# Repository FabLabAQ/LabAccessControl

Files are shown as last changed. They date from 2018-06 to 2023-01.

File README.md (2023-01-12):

# LabAccessControl

## FabLab access and machine control system proof-of-concept
* We use this system to manage access to our laboratory and machines usage (3D printers, laser cutter, CNC mill, etc.).
* Maker friendly and customizable, based on ESP8266 and programmed through the Arduino IDE.
* The ESP retrieves an authorized RFID cards list from a Google sheet and stores that list on flash memory, only when that list changes the internal cards list is updated with minimum flash memory wearing.
* It also logs events (what happened, when, and eventually who) on an internal FIFO and sends these logs to another Google sheet when internet connection is available.
* Due to the features above, this system can work also when internet connection goes down.

# WARNING:
Don't use MIFARE Classic cards if you don't want unauthorized access, they are clonable. Use at least Ultralight C for secure encryption.

# Development
## TODO (urgent)
Common
- [ ] diversify card keys
- [ ] switch to msgpack instead of json

Firmware
- [ ] replace DES library
- [ ] implement DES key generation
- [ ] switch to incremental mode for db updates
- [ ] implement signed messages
- [ ] implement provisioning and recovery of keys (Tang-like)

Script
- [ ] unify sheets
- [ ] incremental updates
- [ ] provisioning and recovery

App
- [ ] signed messages

## Wishlist
- [ ] switch to MQTT
- [ ] full server implmentation
- [ ] code refactoring
- [ ] external crypto chip
- [ ] smartphone nfc auth

Notes:

External crypto chip: should be used to generate card keys through hkdf/hmac, holding the source key securely and allowing it to be used only on successful authentication by the host MCU. The MCU should authenticate by recovering its private key using the procedure described above (Tang-like) or should use encrypted communications with that key.

Smartphone nfc auth: without changing the nfc reader chip (RC522), the only usable mode is host card emulation, which doesn't have a fixed UID, so the authentication protocol must be implemented on top of NDEF messages. For example: first the reader determines it's a smartphone, eventually by reading the ndef message from it, then begins the authentication process in which the reader, writing an NDEF message to the smartphone's emulated card, asks to hash some random data, and once hashed/signed using the phone's private key, that data should be read through another NDEF message and verified using the public key on the reader.

HTTP requests from Android: try retrofit

Test key: `KhGJGmHMHDS0FubbcqiVnAqxoRv1SlqD0Mg/EtXrdb0=`

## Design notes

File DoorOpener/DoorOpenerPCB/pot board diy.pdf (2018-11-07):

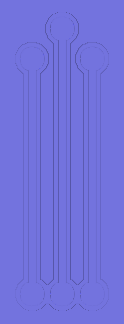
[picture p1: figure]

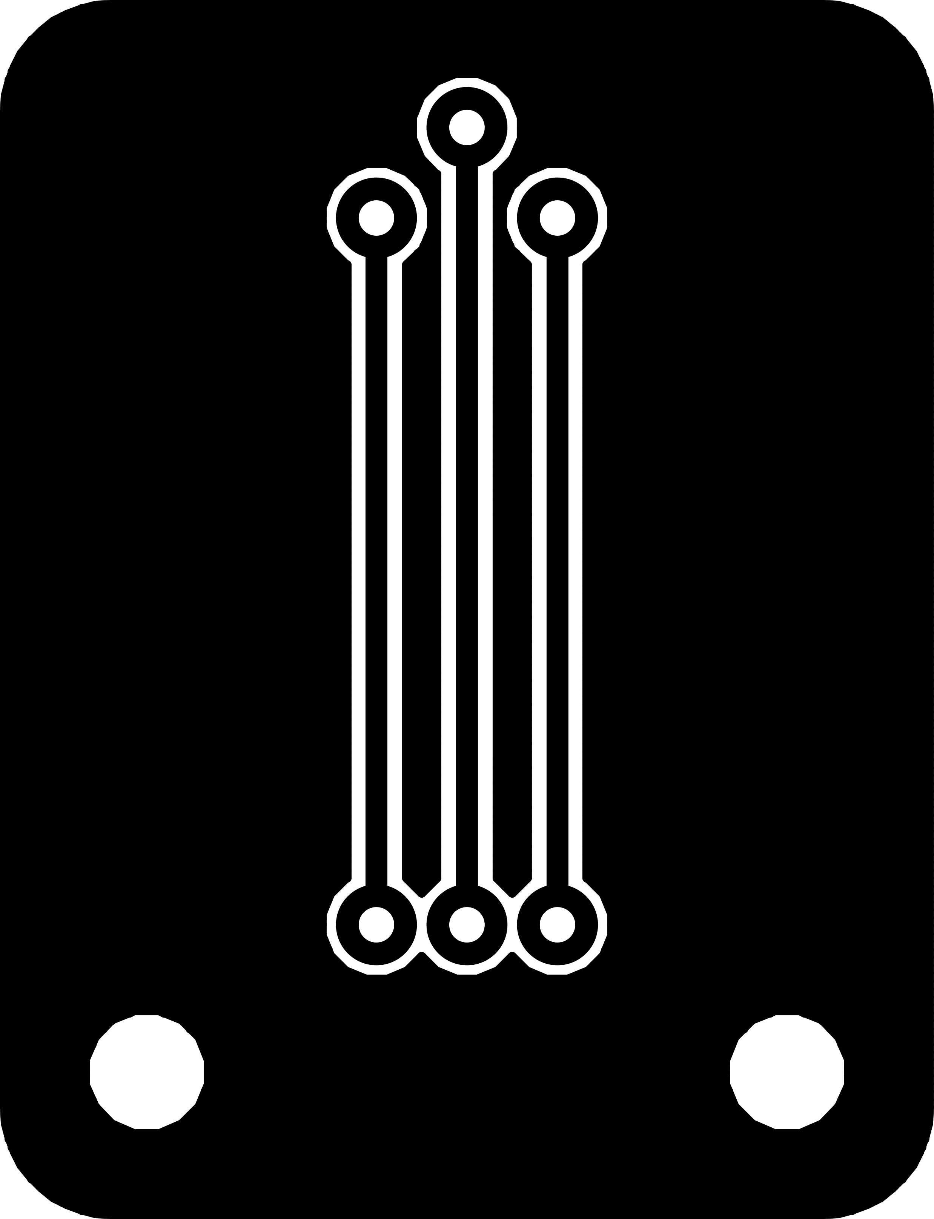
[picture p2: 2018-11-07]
DoorOpener/DoorOpenerPCB/pot board.pdf.png

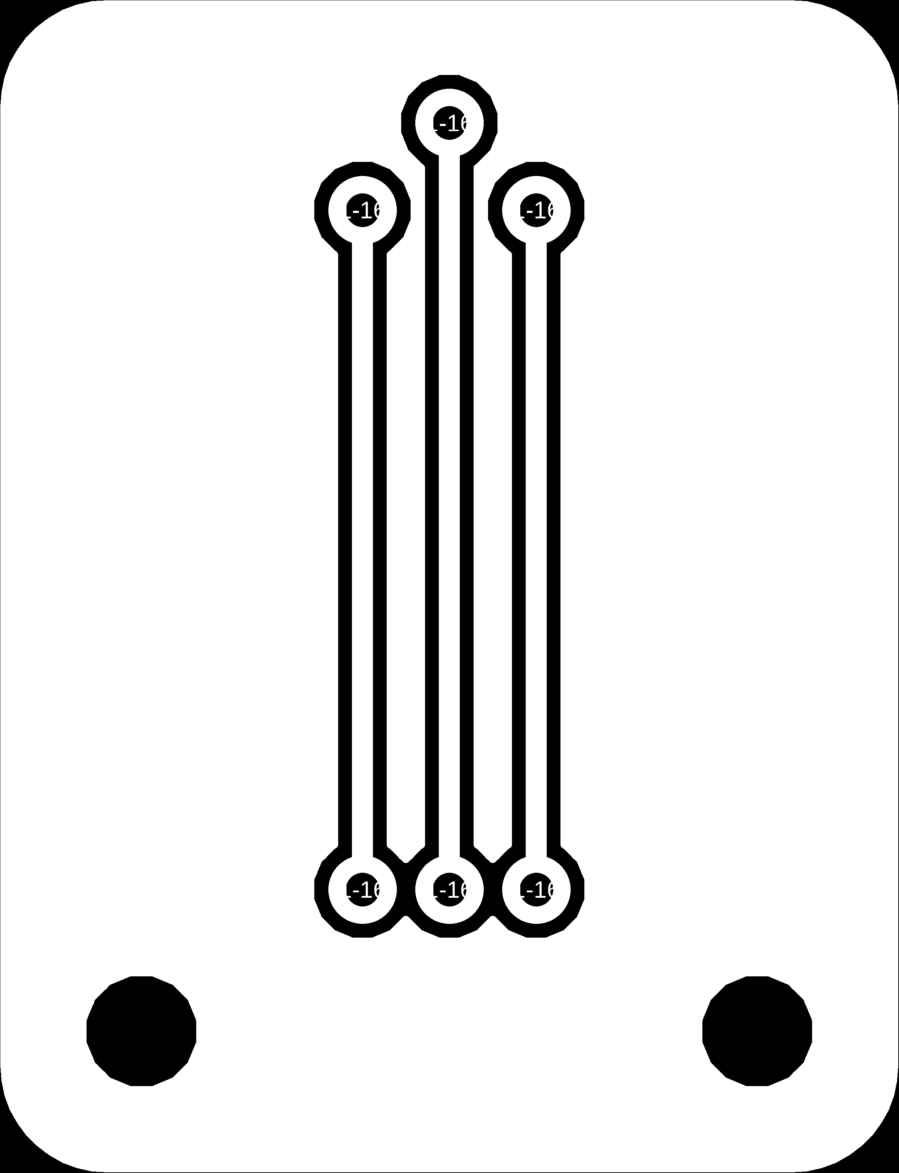
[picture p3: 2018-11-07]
DoorOpener/DoorOpenerPCB/pot board diy.png

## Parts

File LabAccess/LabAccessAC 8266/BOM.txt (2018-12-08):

Minimum setup:
1x ESP-12 module
1x HLK-PM03 power supply
1x SRD-03VDC-SL-C relay
1x 0805 22uF 25V ceramic capacitors
2x 0603 1uF 25V ceramic capacitors
1x 07D391K 7mm 250Vrms varistor
1x 100nF 10mm pitch X2 rated capacitor
1x 10mH 8x10mm inductor (few mA)
1x 500mA 250V axial fuse
1x 1N400x SOD-323 diode or equivalent
1x AO3400 SOT23-3 N-MOSFET or equivalent
1x 0603 2ohm resistor
1x 0603 10k resistor
1x 8p 2.54mm female header
1x 4p 2.54mm male header (or pogo-pins)
1x 3p 5.08mm screw terminal
1x horizontal button

Optional for external switch:
1x 3.5mm 2p screw terminal
3x 0603 0ohm resistors (one marked ROC, two in place of TLP281)
1x 0603 pull-up resistor depending on environment (marked RSW)

Optional for optocoupler setup:
1x TLP281
1x 0603 series resistor depending on input voltage (marked ROC)
1x 0603 pull-up resistor around 1k (marked RSW)

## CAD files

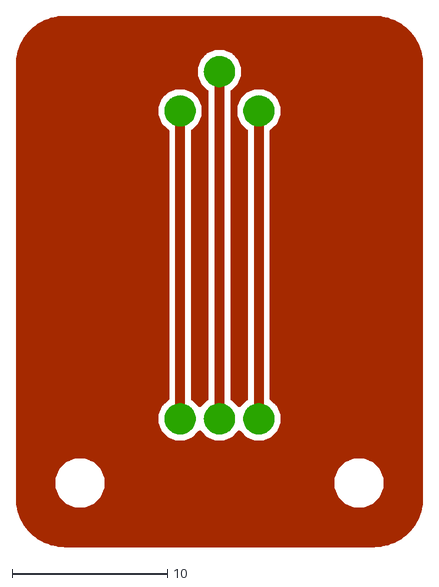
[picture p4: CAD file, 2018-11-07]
DoorOpener/DoorOpenerPCB/pot board diy.dxf
26.3 x 34.3

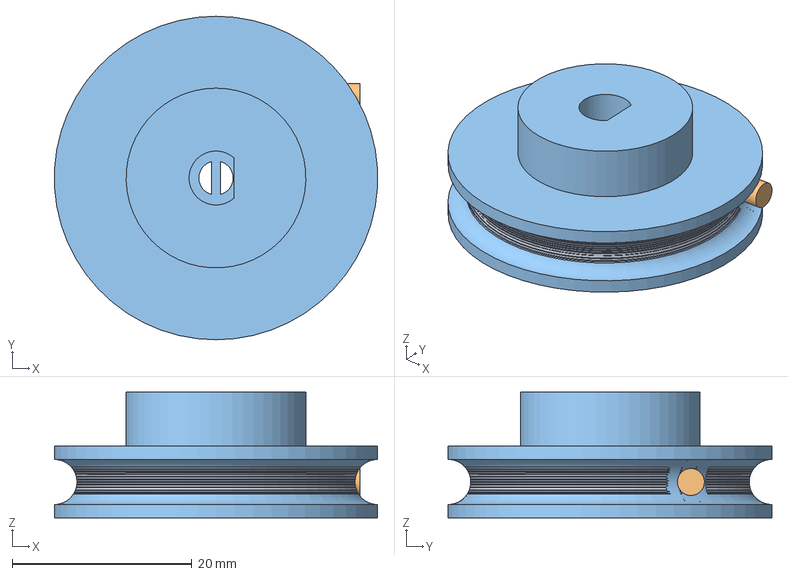
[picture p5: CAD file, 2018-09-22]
DoorOpener/pulley.fcstd
35.9 x 36.0 x 14.0 mm

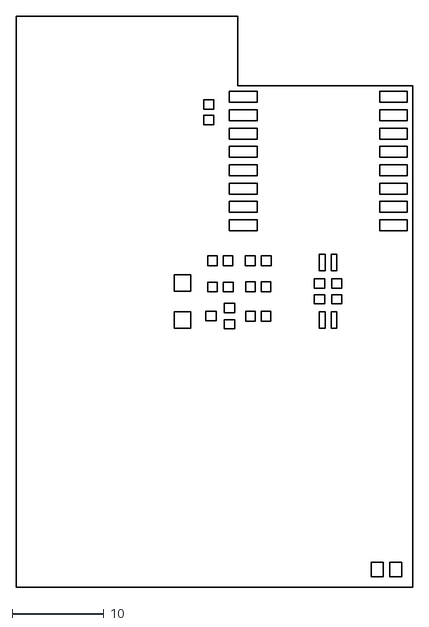
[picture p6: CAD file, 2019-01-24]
LabAccess/LabAccessAC 8266/stencil.dxf
43.1 x 62.2

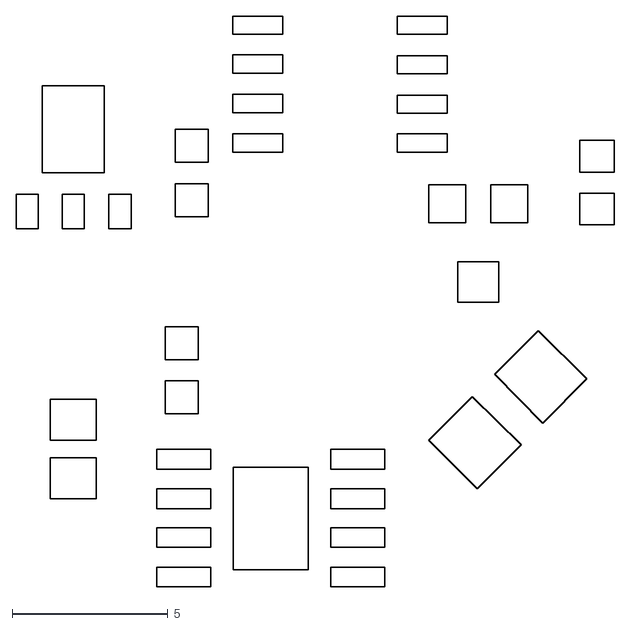
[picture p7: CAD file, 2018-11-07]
DoorOpener/DoorOpenerPCB/DoorOpenerPCBv2.dxf
19.2 x 18.4

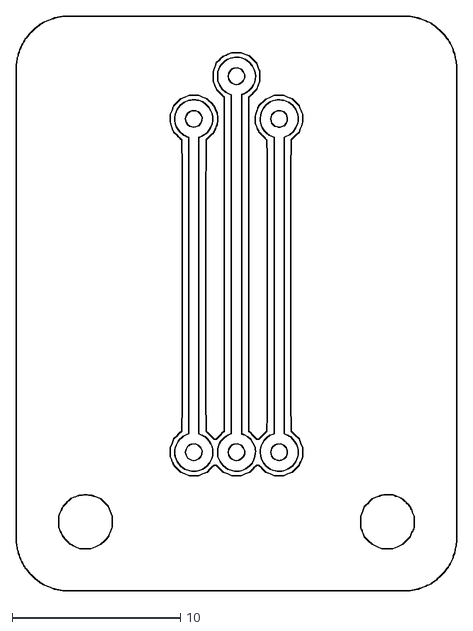
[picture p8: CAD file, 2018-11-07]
DoorOpener/DoorOpenerPCB/pot board.dxf
26.2 x 34.2

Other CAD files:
DoorOpener/pulley.stl

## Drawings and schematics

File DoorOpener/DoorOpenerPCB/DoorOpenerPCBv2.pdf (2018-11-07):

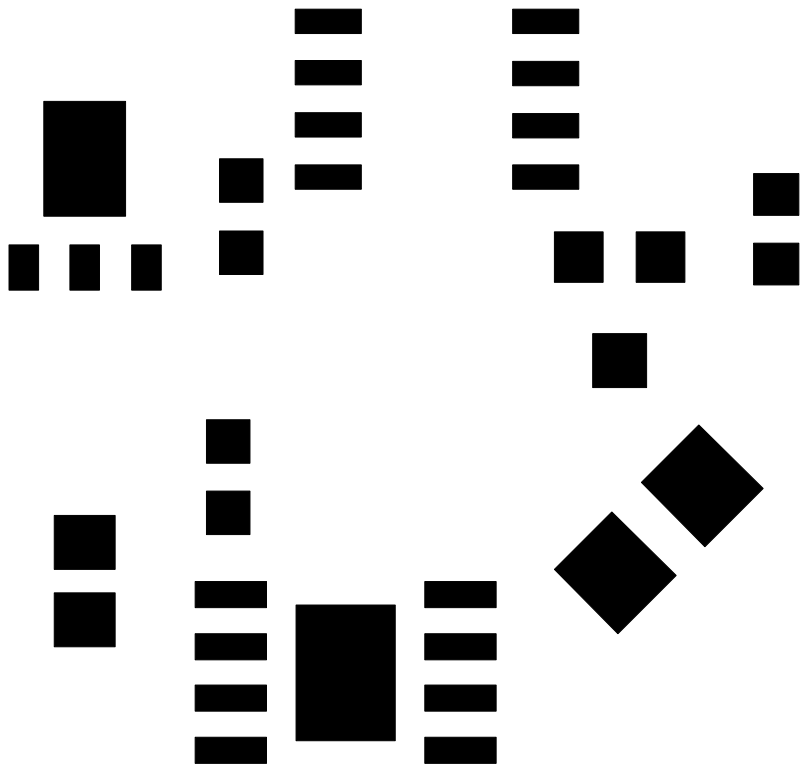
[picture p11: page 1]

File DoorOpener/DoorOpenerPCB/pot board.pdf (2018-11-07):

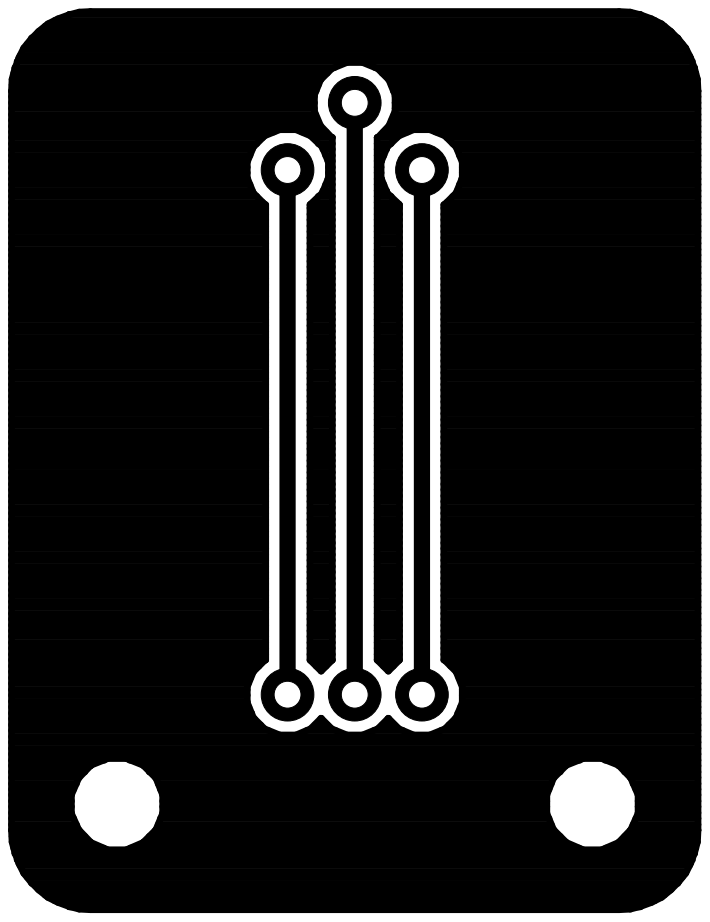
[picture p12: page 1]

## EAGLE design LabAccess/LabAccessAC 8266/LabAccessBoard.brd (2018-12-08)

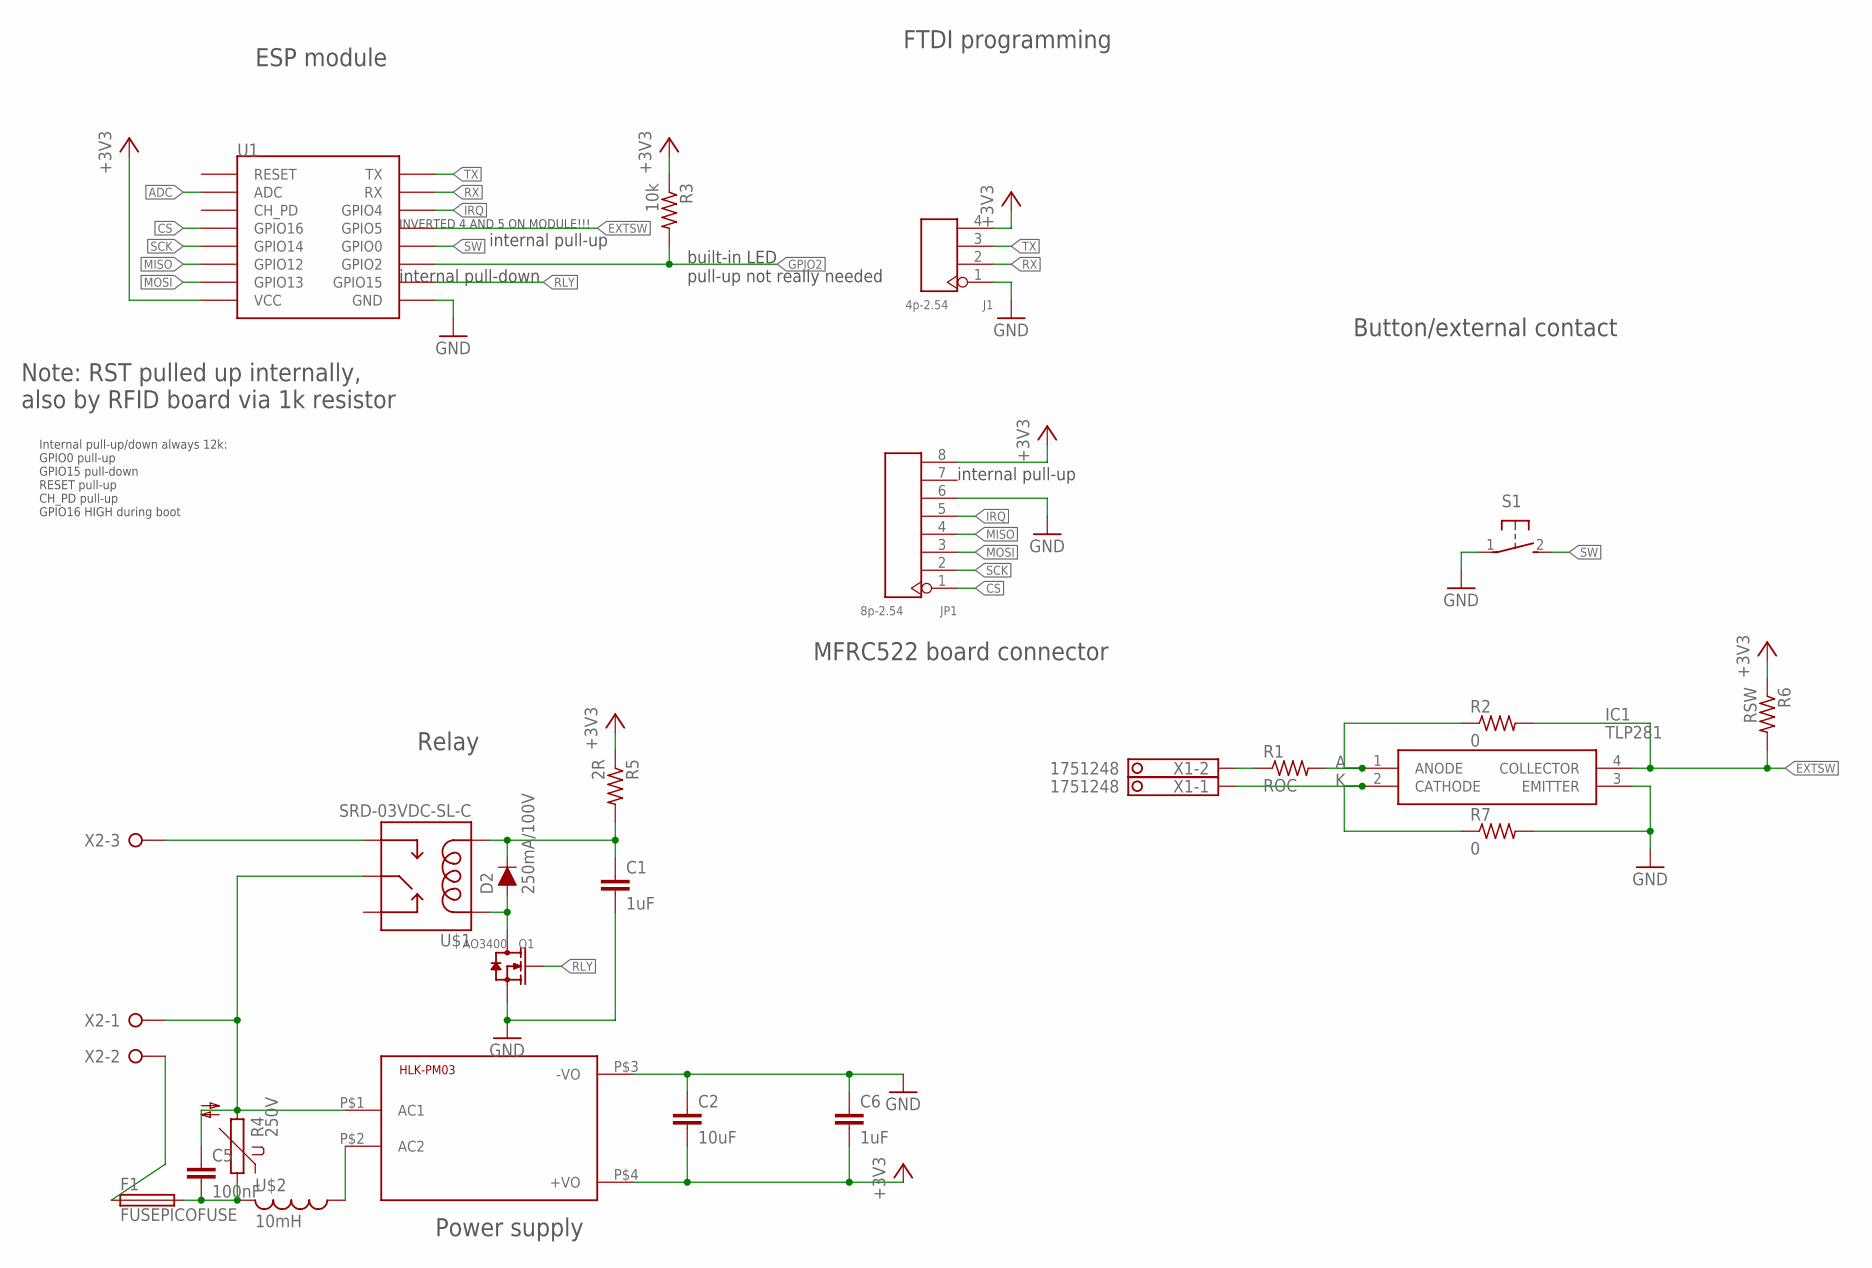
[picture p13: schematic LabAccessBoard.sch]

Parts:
C1, C6: 1uF; C0603K
C2: 10uF; C0805K
C5: 100nF; C102-064X133
D2: 250mA/100V; SOD-323
F1: FUSEPICOFUSE; PICOFUSE
HLK-PM03: HLK-PM03; HLK-PM01
IC1: TLP281; SOIC127P700X190-4N
J1: 4p-2.54; H4-2.54
JP1: 8p-2.54; H8-2.54
Q1: AO3400; SOT-23
R1: ROC; R0603
R2, R7: 0; R0603
R3: 10k; R0603
R4: 250V; S07K250
R5: 2R; R0603
R6: RSW; R0603
S1: 31-XX; B3F-31XX
U1: ESP12SMD; ESP12-SMD
U$1: SRD-03VDC-SL-C; SRD-0XVDC-SL-C
U$2: 10mH; 6000-XXXX-RC
X1: 1751248
X2: W237-3E

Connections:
+3V3: C2.2, C6.2, HLK-PM03.P$4 (+VO), J1.4, JP1.8, R3.1, R5.1, R6.1, U1.VCC
A: IC1.1 (ANODE), R1.2, R2.1
ADC: U1.ADC
CS: JP1.1, U1.GPIO16
EXTSW: IC1.4 (COLLECTOR), R2.2, R6.2, U1.GPIO5
GND: C1.2, C2.1, C6.1, HLK-PM03.P$3 (-VO), IC1.3 (EMITTER), J1.1, JP1.6, Q1.2 (S), R7.2, S1.1, U1.GND
GPIO2: R3.2, U1.GPIO2
IRQ: JP1.5, U1.GPIO4
K: IC1.2 (CATHODE), R7.1, X1.1
MISO: JP1.4, U1.GPIO12
MOSI: JP1.3, U1.GPIO13
unnamed: U$1.SWOPEN, X2.3
unnamed: C5.1, HLK-PM03.P$1 (AC1), R4.2, U$1.SWCOMMON, X2.1
unnamed: C5.2, F1.2, R4.1, U$2.2
unnamed: F1.1, X2.2
unnamed: C1.1, D2.C, R5.2, U$1.COIL0
unnamed: HLK-PM03.P$2 (AC2), U$2.1
unnamed: D2.A, Q1.3 (D), U$1.COIL1
unnamed: R1.1, X1.2
RLY: Q1.1 (G), U1.GPIO15
RX: J1.2, U1.RXD0 (RX)
SCK: JP1.2, U1.GPIO14
SW: S1.2 (S), U1.GPIO0
TX: J1.3, U1.TXD0 (TX)

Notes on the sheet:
ESP module
Note: RST pulled up internally, also by RFID board via 1k resistor
FTDI programming
Button/external contact
MFRC522 board connector
Power supply
Relay
built-in LED pull-up not really needed
internal pull-down
internal pull-up
INVERTED 4 AND 5 ON MODULE!!!
Internal pull-up/down always 12k: GPIO0 pull-up GPIO15 pull-down RESET pull-up CH_PD pull-up GPIO16 HIGH during boot

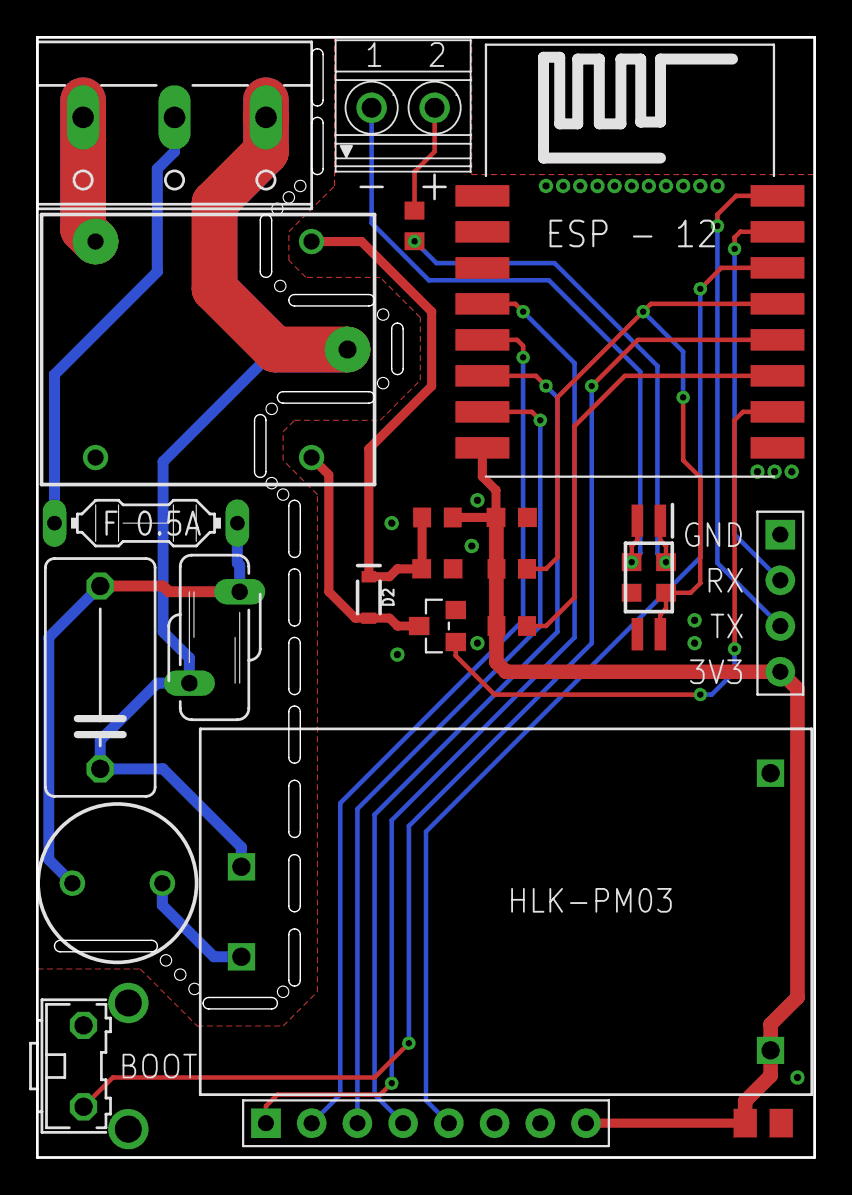
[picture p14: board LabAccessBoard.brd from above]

Board: 2 copper layers, 43.2 x 62.2 mm, 25 parts (1 on the bottom side), 23 nets.

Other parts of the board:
U$3: OSHW-LOGO-L

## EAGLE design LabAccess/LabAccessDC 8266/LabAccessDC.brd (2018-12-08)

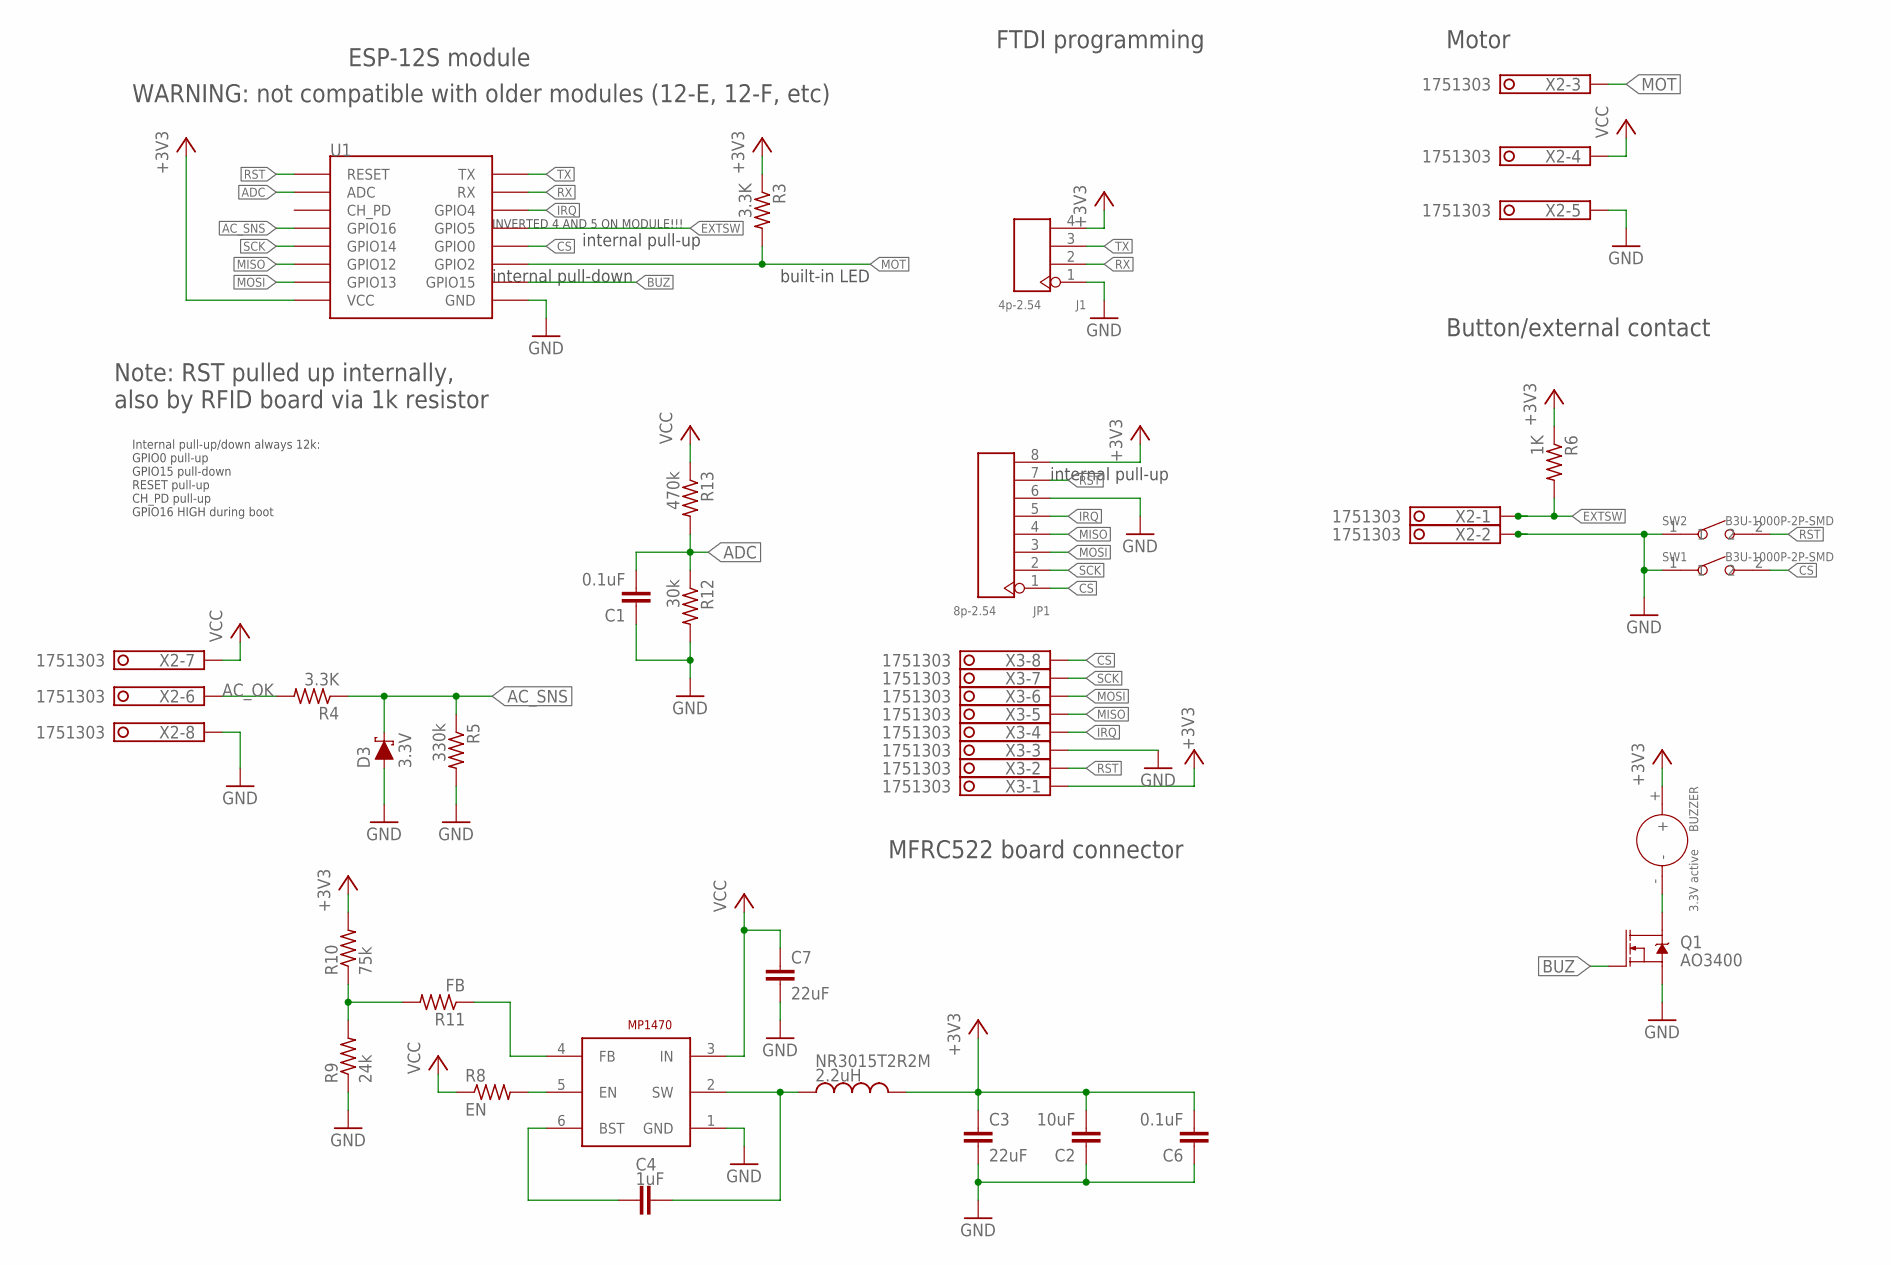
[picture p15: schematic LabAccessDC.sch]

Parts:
BUZZER: 3.3V active; BZ2-7.6-D12.0XH6.5MM
C1, C6: 0.1uF; C0603K
C2: 10uF; C0805K
C3, C7: 22uF; C0805K
C4: 1uF; C0603K
D3: 3.3V; SPARKFUN-DISCRETESEMI_SOD-523
J1: 4p-2.54; H4-2.54
JP1: 8p-2.54; H8-2.54
MP1470: MP1470GJ; TSOT-23-6
NR3015T2R2M: 2.2uH; INDUCTOR-NR3015
Q1: AO3400; SOT23-3
R3, R4: 3.3K; R0603
R5: 330k; R0603
R6: 1K; R0603
R8: EN; R0603
R9: 24k; R0603
R10: 75k; R0603
R11: FB; R0603
R12: 30k; R0603
R13: 470k; R0603
SW1, SW2: B3U-1000P-2P-SMD; SW2-2.6-3.0X2.5X1.2+0.4MM
U1: ESP12SMD; ESP12-SMD
X2, X3: 1751303

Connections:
+3V3: BUZZER.+, C2.2, C3.1, C6.2, J1.4, JP1.8, NR3015T2R2M.2, R3.1, R6.1, R10.2, U1.VCC, X3.1
AC_OK: R4.2, X2.6
AC_SNS: D3.C, R4.1, R5.1, U1.GPIO16
ADC: C1.2, R12.1, R13.2, U1.ADC
BUZ: Q1.1 (G), U1.GPIO15
CS: JP1.1, SW1.2, U1.GPIO0, X3.8
EXTSW: R6.2, U1.GPIO5, X2.1
GND: C1.1, C2.1, C3.2, C6.1, C7.2, D3.A, J1.1, JP1.6, MP1470.1 (GND), Q1.2 (S), R5.2, R9.1, R12.2, SW1.1, SW2.1, U1.GND, X2.2, X2.5, X2.8, X3.3
IRQ: JP1.5, U1.GPIO4, X3.4
MISO: JP1.4, U1.GPIO12, X3.5
MOSI: JP1.3, U1.GPIO13, X3.6
MOT: R3.2, U1.GPIO2, X2.3
unnamed: BUZZER.-, Q1.3 (D)
unnamed: C4.1, MP1470.6 (BST)
unnamed: C4.2, MP1470.2 (SW), NR3015T2R2M.1
unnamed: MP1470.5 (EN), R8.2
unnamed: R9.2, R10.1, R11.2
unnamed: MP1470.4 (FB), R11.1
RST: JP1.7, SW2.2, U1.RESET, X3.2
RX: J1.2, U1.RXD0 (RX)
SCK: JP1.2, U1.GPIO14, X3.7
TX: J1.3, U1.TXD0 (TX)
VCC: C7.1, MP1470.3 (IN), R8.1, R13.1, X2.4, X2.7

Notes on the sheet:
ESP-12S module
Note: RST pulled up internally, also by RFID board via 1k resistor
FTDI programming
Button/external contact
MFRC522 board connector
built-in LED
internal pull-down
internal pull-up
INVERTED 4 AND 5 ON MODULE!!!
Internal pull-up/down always 12k: GPIO0 pull-up GPIO15 pull-down RESET pull-up CH_PD pull-up GPIO16 HIGH during boot
Motor
WARNING: not compatible with older modules (12-E, 12-F, etc)

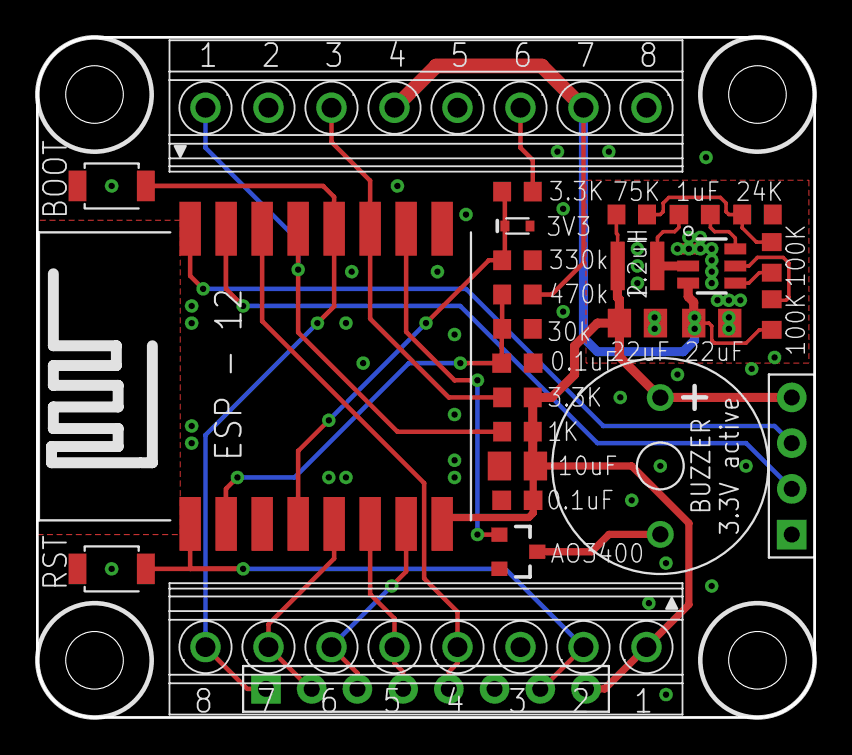
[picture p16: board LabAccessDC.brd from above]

Board: 2 copper layers, 43.2 x 37.8 mm, 29 parts (1 on the bottom side), 23 nets.

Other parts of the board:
U$3: OSHW-LOGO-L

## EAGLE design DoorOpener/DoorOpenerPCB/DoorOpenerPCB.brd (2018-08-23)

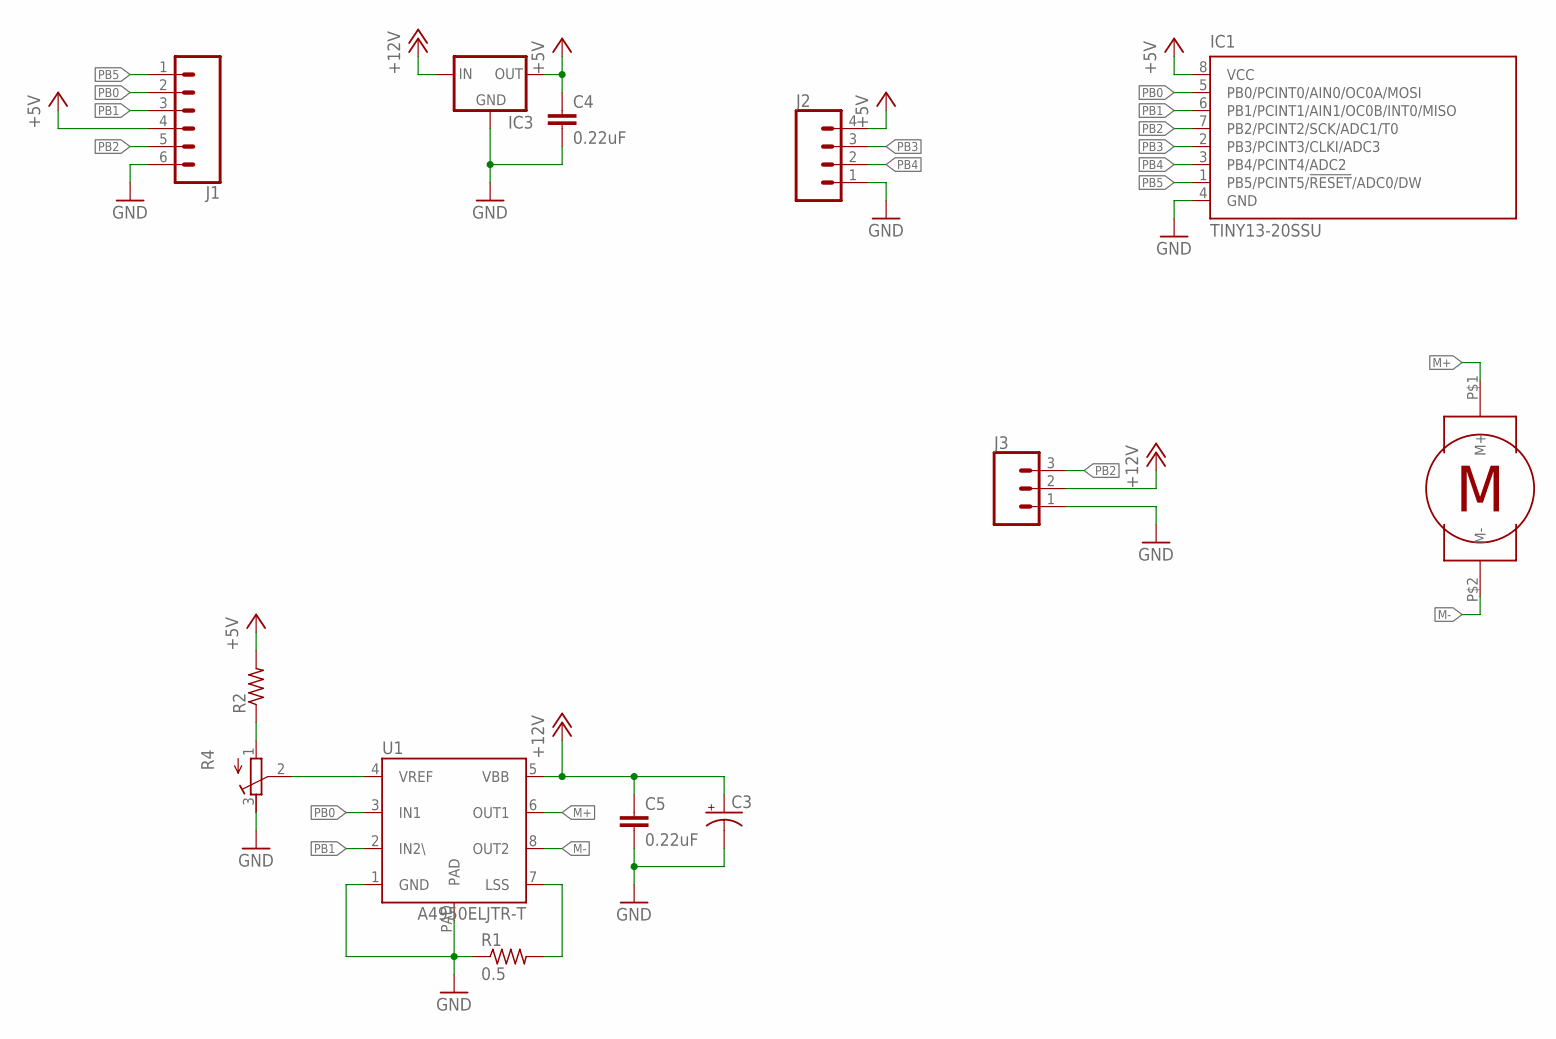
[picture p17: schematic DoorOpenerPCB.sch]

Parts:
C3: CPOL-USCT3528; CT3528
C4, C5: 0.22uF; C0603K
IC1: TINY13-20SSU; 8S1
IC3: 78LXX-SOT89R; SOT89R
J1: CONN_061.27MM; 1X06_1.27MM
J2: CONN_041.27MM; 1X04_1.27MM
J3: CONN_03JST-PTH-NS; JST-3-PTH-NS
R1: 0.5; R0805
R2: R-US_R0603; R0603
R4: R-TRIMM3103; RTRIM3103
U1: A4950ELJTR-T; SOIC8TP
U$2: JGY-370; PKG

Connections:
+5V: C4.1, IC1.8 (VCC), IC3.2 (OUT), J1.4, J2.4, R2.2
+12V: C3.+, C5.1, IC3.1 (IN), J3.2, U1.5 (VBB)
GND: C3.-, C4.2, C5.2, IC1.4 (GND), IC3.3 (GND), IC3.4 (GND), J1.6, J2.1, J3.1, R1.1, R4.3 (E), U1.1 (GND), U1.PAD
M+: U1.6 (OUT1), U$2.P$1 (M+)
M-: U1.8 (OUT2), U$2.P$2 (M-)
unnamed: R4.2 (S), U1.4 (VREF)
unnamed: R1.2, U1.7 (LSS)
unnamed: R2.1, R4.1 (A)
PB0: IC1.5 (PB0/PCINT0/AIN0/OC0A/MOSI), J1.2, U1.3 (IN1)
PB1: IC1.6 (PB1/PCINT1/AIN1/OC0B/INT0/MISO), J1.3, U1.2 (IN2\)
PB2: IC1.7 (PB2/PCINT2/SCK/ADC1/T0), J1.5, J3.3
PB3: IC1.2 (PB3/PCINT3/CLKI/ADC3), J2.3
PB4: IC1.3 (PB4/PCINT4/ADC2), J2.2
PB5: IC1.1 (PB5/PCINT5/!RESET!/ADC0/DW), J1.1

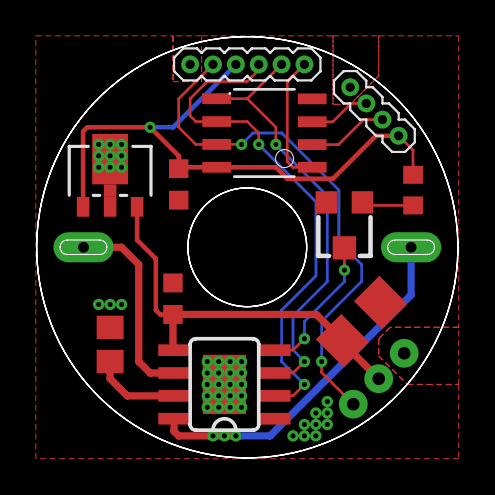
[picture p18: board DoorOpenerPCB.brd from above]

Board: 2 copper layers, 23.4 x 23.4 mm, 13 parts (0 on the bottom side), 14 nets.

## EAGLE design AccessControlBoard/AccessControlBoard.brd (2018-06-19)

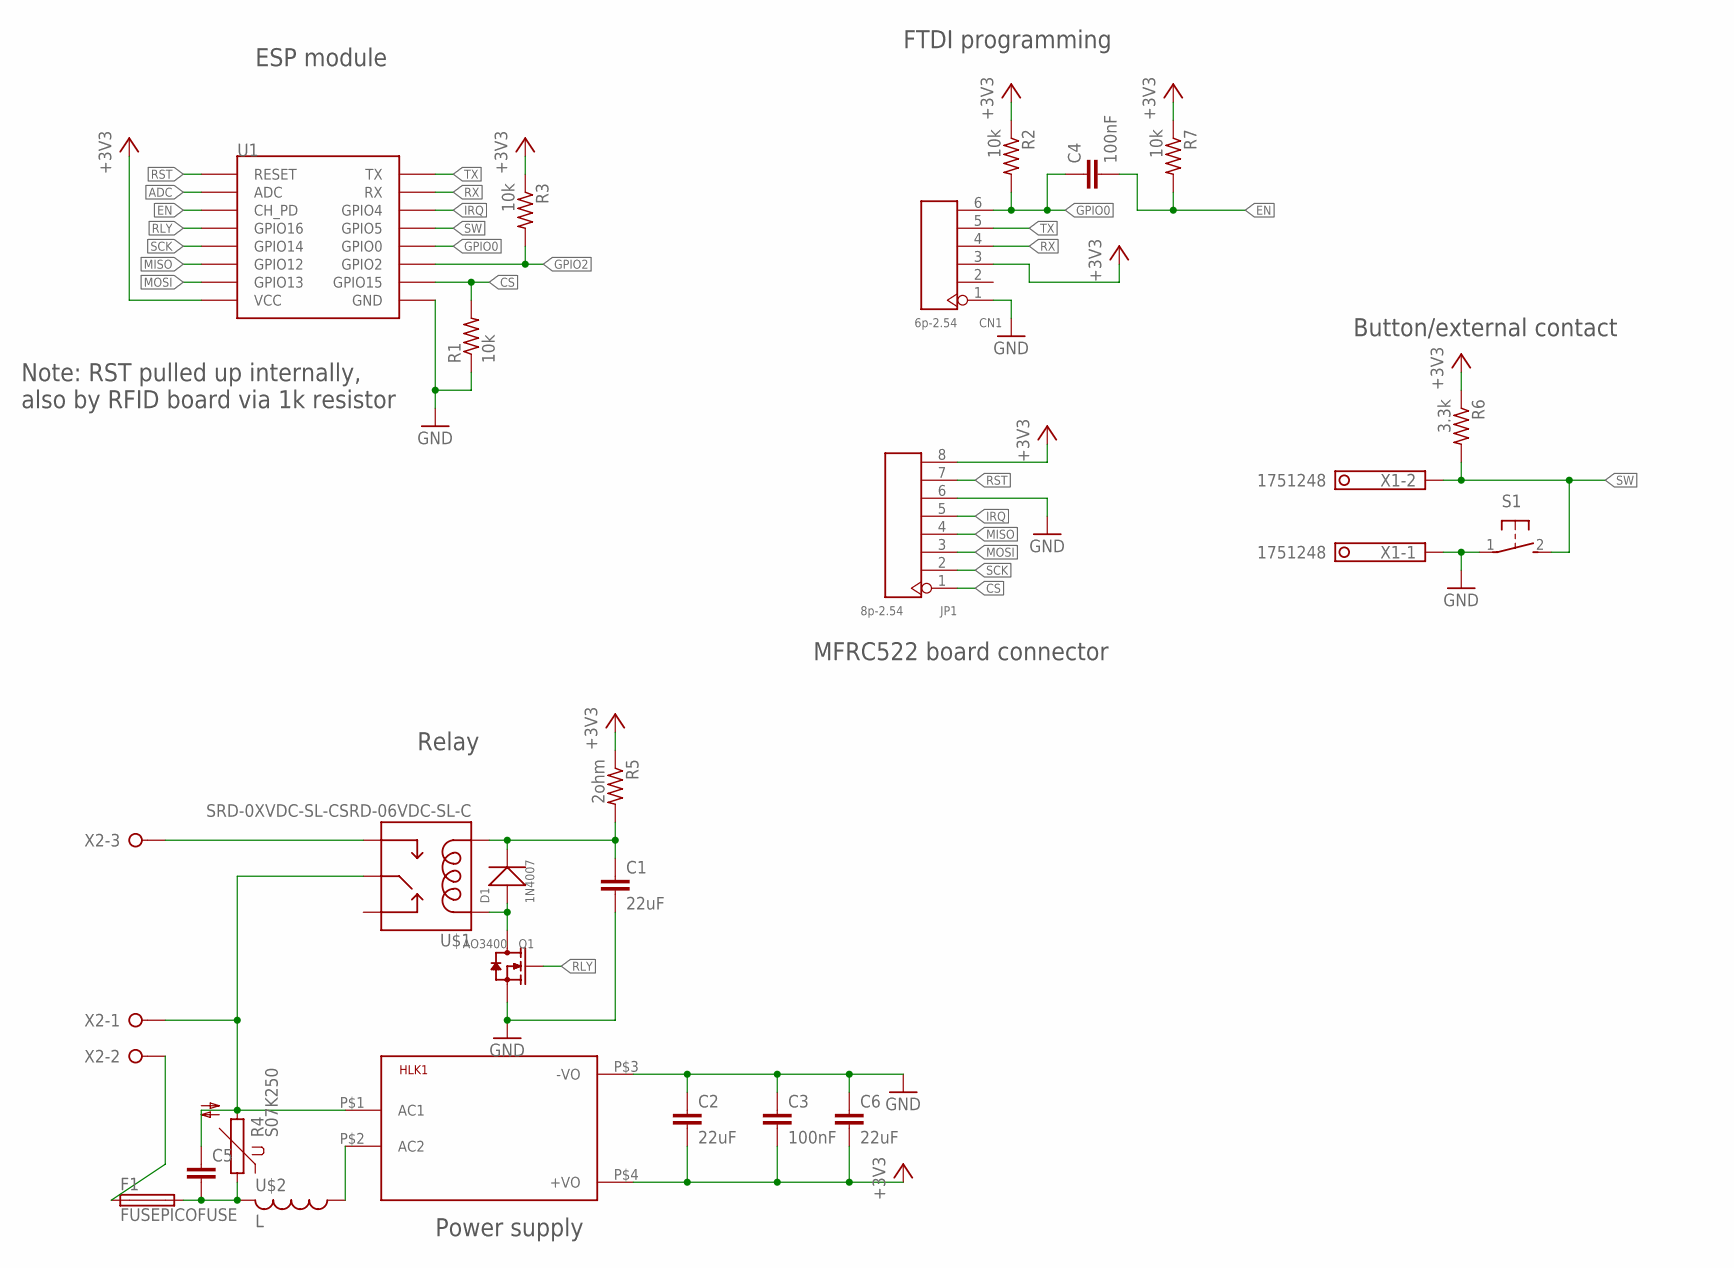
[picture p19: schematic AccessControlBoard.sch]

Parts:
C1, C2, C6: 22uF; C0805K
C3, C4: 100nF; C0603K
C5: C-EU102-064X133; C102-064X133
CN1: 6p-2.54; H6-2.54
D1: 1N4007; DO-214AC
F1: FUSEPICOFUSE; PICOFUSE
HLK1: HLK-PM013W; HLK-PM01
JP1: 8p-2.54; H8-2.54
Q1: AO3400; SOT-23
R1, R2, R3, R7: 10k; R0603
R4: S07K250
R5: 2ohm; R0603
R6: 3.3k; R0603
S1: 31-XX; B3F-31XX
U1: ESP12SMD; ESP12-SMD
U$1: SRD-0XVDC-SL-CSRD-06VDC-SL-C; SRD-0XVDC-SL-C
U$2: L; 6000
X1: 1751248
X2: W237-3E

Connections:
+3V3: C2.2, C3.2, C6.2, CN1.3, HLK1.P$4 (+VO), JP1.8, R2.1, R3.1, R5.1, R6.1, R7.1, U1.VCC
ADC: U1.ADC
CS: JP1.1, R1.2, U1.GPIO15
EN: C4.2, R7.2, U1.CH_PD
GND: C1.2, C2.1, C3.1, C6.1, CN1.1, HLK1.P$3 (-VO), JP1.6, Q1.2 (S), R1.1, S1.1, U1.GND, X1.1
GPIO0: C4.1, CN1.6, R2.2, U1.GPIO0
GPIO2: R3.2, U1.GPIO2
IRQ: JP1.5, U1.GPIO4
MISO: JP1.4, U1.GPIO12
MOSI: JP1.3, U1.GPIO13
unnamed: U$1.SWOPEN, X2.3
unnamed: C5.1, HLK1.P$1 (AC1), R4.2, U$1.SWCOMMON, X2.1
unnamed: C5.2, F1.2, R4.1, U$2.2
unnamed: F1.1, X2.2
unnamed: C1.1, D1.2 (-), R5.2, U$1.COIL0
unnamed: HLK1.P$2 (AC2), U$2.1
unnamed: D1.1 (+), Q1.3 (D), U$1.COIL1
RLY: Q1.1 (G), U1.GPIO16
RST: JP1.7, U1.RESET
RX: CN1.4, U1.RXD0 (RX)
SCK: JP1.2, U1.GPIO14
SW: R6.2, S1.2 (S), U1.GPIO5, X1.2
TX: CN1.5, U1.TXD0 (TX)

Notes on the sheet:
ESP module
Note: RST pulled up internally, also by RFID board via 1k resistor
FTDI programming
Button/external contact
MFRC522 board connector
Power supply
Relay

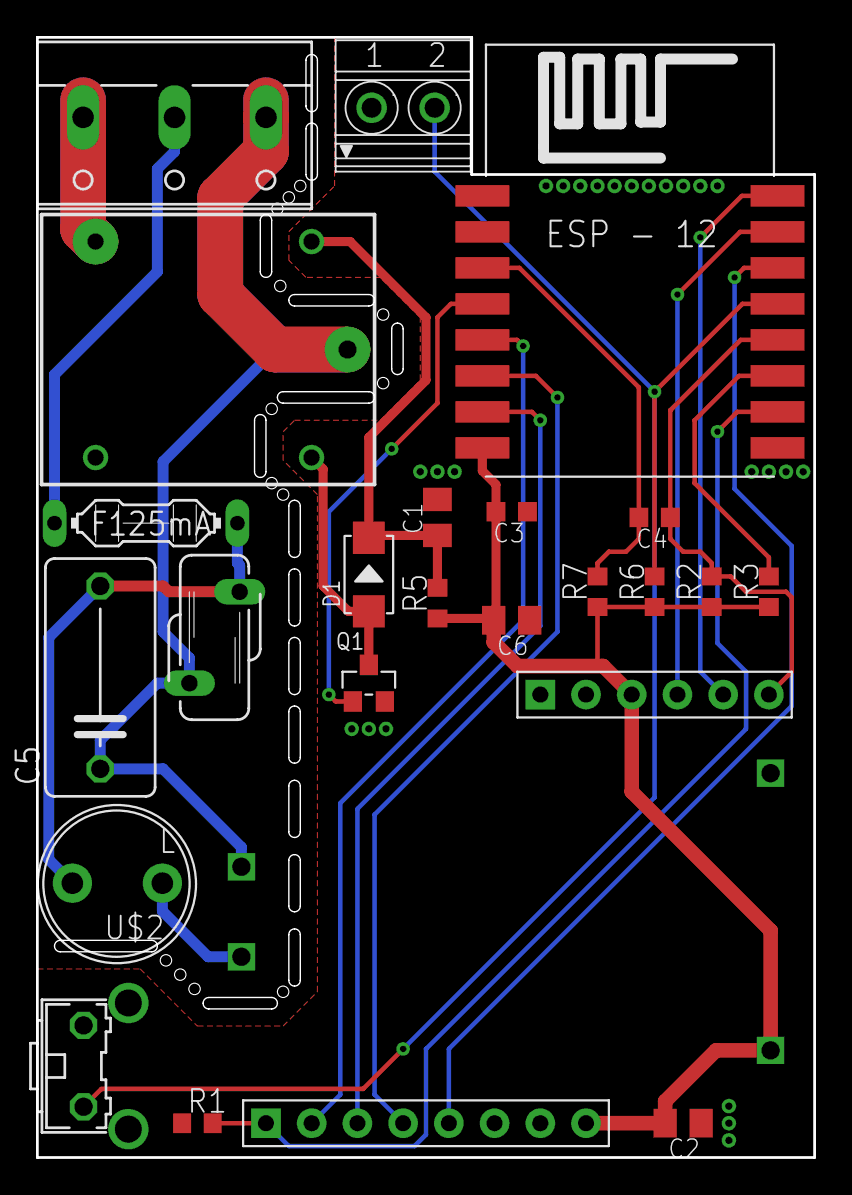
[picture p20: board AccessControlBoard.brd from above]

Board: 2 copper layers, 43.2 x 62.2 mm, 26 parts (1 on the bottom side), 22 nets.

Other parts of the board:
U$3: OSHW-LOGO-L

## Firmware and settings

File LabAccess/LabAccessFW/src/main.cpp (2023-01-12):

/*
 * Lab Access System
 * (c) 2018 Luca Anastasio
 * anastasio.lu@gmail.com
 * www.fablaquila.org
 *
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
 */

#include <Arduino.h>
#include <ESP8266WiFi.h>
#include "constants.h"
#include <ArduinoOTA.h>
#include <SPI.h>
#include <TrueRandom.h>
#include <Bounce2.h>
// #include <FS.h>
#include <LittleFS.h>
#include "Card_DB.h"

#include <HTTPSRedirect.h>
#include "logging.h"
#include <time.h>
#include <sys/time.h>
#include <LabAccessOTA.h>
#include <LabAccessWiFi.h>
#include "MifareUltralight.h"
#include "config.h"
// #include <coredecls.h>

#define DEBUG_FLAG "MAIN"
#include "debug.h"

MifareUltralight RFID;
Bounce ext_sw, int_sw, set_sw;

void setup()
{
	LA_DSTART(115200);
	setupWiFi();
#ifdef LAB_ACCESS_DEBUG
	redirect.setInsecure();
	redirect.setPrintResponseBody(true);
#else
	redirect.setPrintResponseBody(false);
#endif
	setupOTA();
#ifdef LAB_ACCESS_DEBUG
	String fs = "FS files list: \n";
	Dir dir = LittleFS.openDir("");
	while (dir.next())
	{
		fs += "\t" + dir.fileName() + "\n";
	}
	LA_DPRINTF("%s", fs.c_str());
#endif
	// Input/Output
	/* TODO: implement interrupt driven version
	 * pinMode(pin.irq, INPUT_PULLUP);
	 * attachInterrupt(digitalPinToInterrupt(pin.irq), ???, FALLING);
	 */
	pinMode(pin.out, OUTPUT);
	pinMode(pin.led, OUTPUT);
	ext_sw.attach(pin.esw);
	ext_sw.interval(extsw_deb_time);
	// int_sw.attach(pin.isw);
	// int_sw.interval(intsw_deb_time);
	set_sw.attach(0);
	set_sw.interval(setsw_deb_time);
	RFID.SetKey(nfc_key, true);
	SPI.begin();
	// SPI.setHwCs(true);
	RFID.PCD_Init(pin.csn, pin.rst);
// RFID.PCD_SetAntennaGain(Ultralight.RxGain_max);
#ifdef LAB_ACCESS_DEBUG
	RFID.PCD_DumpVersionToSerial();
#endif
	LA_DPRINTF("Waiting for time sync\n");
	time_t now = 0;
	while ((now = time(NULL)) < COMPILE_TIME) {
		delay(1000);
		configTime(TZ_SEC, DST_SEC, NTP_server_address);
	}
	LA_DPRINTF("Time updated: %s\n", ctime(&now));
	LOG(LOG_MSG_BOARD_BOOT);
	LA_DPRINTF("Setup completed\n");
}

void wait_for_new_card(MifareUltralight::Uid old_uid)
{
	while (strncmp((char *)RFID.uid.uidByte, (char *)old_uid.uidByte, 7) == 0)
	{
		if (RFID.PICC_IsNewCardPresent())
		{
			RFID.PICC_ReadCardSerial();
		}
	}
}

int auth_card()
{
	if (!RFID.PICC_IsNewCardPresent())
		return 1;
	if (!RFID.PICC_ReadCardSerial())
	{
		LA_DPRINTF("Failed to read card serial\n");
		return -1;
	}
#ifdef LAB_ACCESS_DEBUG
	RFID.PICC_DumpDetailsToSerial(&RFID.uid);
#endif
	delayMicroseconds(TrueRandomGet32() & 0x00000FFF);
	LA_DPRINTF("New card detected, authenticating...\n");
	RFID.dump(&RFID.uid);
	MifareUltralight::StatusCode status = RFID.Authenticate();
	RFID.PICC_HaltA();
	// reactivate the card and retry?
	// byte bufferATQA[2];
	// byte bufferSize = sizeof(bufferATQA);
	// Ultralight.PICC_WakeupA(bufferATQA, &bufferSize);
	// Ultralight.PICC_ReadCardSerial();
	if (status != MifareUltralight::STATUS_OK)
	{
		char buf[48];
		const __FlashStringHelper *cname = RFID.GetStatusCodeName(status);
		strcpy_P(buf, (const char *)cname);
		LA_DPRINTF("Authentication failed: %s\n", buf);
		return -1;
	}
	delayMicroseconds(TrueRandomGet32() & 0x00000FFF);
	if (!cardExistsInDB(RFID.uid.uidByte))
	{
		LA_DPRINTF("Card not found in DB\n");
		return -1;
	}
	return 0;
}

void loop()
{
	wm.process();
	handleOTA();
	static bool authenticated = false;
	static unsigned long lastUpdate = millis();

	static uint32_t tprint = millis();
	if (millis() > tprint + 1000)
	{
		LA_DPRINTF("Free heap %u free stack %u\n", ESP.getFreeHeap(), ESP.getFreeContStack());
		tprint = millis();
	}

	if (millis() > updateInterval + lastUpdate)
	{
		reconnect();
		updateDB();
		if (dev_mode == LA_MODE_DOOR)
		{
			digitalWrite(pin.out, LOW);
			digitalWrite(pin.led, HIGH);
			authenticated = false;
		}
		lastUpdate = millis();
	}

	static unsigned long lastLog = millis();
	if (millis() > updateInterval + lastLog)
	{
		LOG();
		lastLog = millis();
	}

	static unsigned long lastCheck = millis();
	if (millis() > cardCheckDelay + lastCheck)
	{
		int res = auth_card();
		if (res == 0)
		{
			// card authentication succeeded
			digitalWrite(pin.out, HIGH);
			digitalWrite(pin.led, LOW);
			if (dev_mode == LA_MODE_DOOR)
			{
				authenticated = true;
				lastUpdate = millis();
			}
			LOG(LOG_MSG_AUTH_SUCCESS, RFID.uid.uidByte);
		}
		else if (res == -1)
		{
			LOG(LOG_MSG_AUTH_ERROR);
		}
		else
		{
			// no card
		}
		lastCheck = millis();
	}

	ext_sw.update();
	// if the door closes or the switch is pressed
	if (ext_sw.fell())
	{
		if (dev_mode == LA_MODE_DOOR)
		{
			LOG(LOG_MSG_CLOSED_DOOR);
		}
		else
		{
			LOG(LOG_MSG_PRESSED_SWITCH);
			digitalWrite(pin.out, LOW);
			digitalWrite(pin.led, HIGH);
			authenticated = false;
		}
	}
	// else if the door opens
	else if (ext_sw.rose() && (dev_mode == LA_MODE_DOOR))
	{
		if (authenticated)
		{
			LOG(LOG_MSG_OPEN_DOOR_AUTH);
		}
		else
		{
			LOG(LOG_MSG_OPEN_DOOR_NOAUTH);
		}
		digitalWrite(pin.out, LOW);
		digitalWrite(pin.led, HIGH);
		authenticated = false;
	}

	set_sw.update();
	if (set_sw.fell())
	{
		LA_DPRINTF("Entering setup\n");
		conf_done = false;
		redirect.stopAll();
		LA_DPRINTF("Free heap %u free stack %u\n", ESP.getFreeHeap(), ESP.getFreeContStack());
		while (!conf_done)
		{
			wm.startConfigPortal(dev_name.c_str(), ap_key.c_str());
			wait_config();
		}
		ESP.restart();
	}
}

#undef DEBUG_FLAG

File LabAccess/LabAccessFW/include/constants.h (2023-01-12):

/*
 * Lab Access System
 * (c) 2018 Luca Anastasio
 * anastasio.lu@gmail.com
 * www.fablaquila.org
 *
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
 */

#ifndef SETTINGS_H_
#define SETTINGS_H_

#include "Arduino.h"
#include "HTTPSRedirect.h"

#define PGM_STR const char * //PROGMEM //__attribute__((aligned(4)))

#define PIN_INTERRUPT 4
#define PIN_EXTSW 5
#define PIN_RELAY 15
#define PIN_SWITCH 0
#define PIN_LED 2
#define PIN_CS 16
const int extsw_deb_time = 500;
const int intsw_deb_time = 100;
#ifdef LAB_ACCESS_DEBUG
const int setsw_deb_time = 1000;
#else
const int setsw_deb_time = 10000;
#endif

PGM_STR LOG_MSG_BOARD_BOOT = "Board booted successfully";
PGM_STR LOG_MSG_SERVER_RECONNECTION = "Server reconnected";
PGM_STR LOG_MSG_AUTH_SUCCESS = "Authentication successful";
PGM_STR LOG_MSG_AUTH_ERROR = "Authentication ERROR";
PGM_STR LOG_MSG_CLOSED_DOOR = "Door closed";
PGM_STR LOG_MSG_PRESSED_SWITCH = "Machine turned OFF";
PGM_STR LOG_MSG_OPEN_DOOR_AUTH = "Door opened with authentication";
PGM_STR LOG_MSG_OPEN_DOOR_NOAUTH = "Door opened WITHOUT authentication";
PGM_STR LOG_MSG_DB_UPDATED = "Card database updated";

const uint32_t minimum_free_heap = 4000;
const unsigned long updateInterval = 90000, cardCheckDelay = 500;
const uint32_t http_update_led_blink = 200;
HTTPSRedirect redirect(443);
const char script_server_host[] = "script.google.com";
//PGM_STR logScriptURL[] = "/macros/s/" SECRET_LOG_SCRIPT_ID "/exec?log";
//PGM_STR accessScriptURL[] = "/macros/s/" SECRET_ACCESS_SCRIPT_ID "/exec?boardName=" BOARD_NAME;

// script API commands
PGM_STR api_key_prov = "keyProv";
PGM_STR api_key_rec = "keyRec";


static const char* config_filename = "config.json";
const uint16_t config_size = 1024;

const char NTP_server_address[] = "pool.ntp.org";
#define TZ              1       // (utc+) TZ in hours
#define DST_MN          60
#define TZ_MN           ((TZ)*60)
#define TZ_SEC          ((TZ)*3600)
#define DST_SEC         ((DST_MN)*60)

#endif /* SETTINGS_H_ */

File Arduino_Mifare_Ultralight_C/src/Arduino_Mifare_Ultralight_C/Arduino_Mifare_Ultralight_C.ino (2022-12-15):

/*
 * (c) 2019 Luca Anastasio
 * anastasio.lu@gmail.com
 * www.fablaquila.org
 *
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
 */

#include <SPI.h>
//#include <MFRC522.h>

#include "MifareUltralight.h"

#if defined(ESP8266)
#define SS_PIN 15
#define RST_PIN 255
#define LED_PIN 2
#define LED_ON 0
#else

#endif

#define LED_OFF !LED_ON

MifareUltralight Ultralight(SS_PIN, RST_PIN);  // Create MFRC522 instance

// 425245414b4d454946594f5543414e21

const uint8_t n_keys = 3;
const uint8_t defaultKeys[n_keys][16] = {
	{'B','R','E','A','K','M','E','I','F','Y','O','U','C','A','N','!'},
	{0  ,0  ,0  ,0  ,0  ,0  ,0  ,0  ,0  ,0  ,0  ,0  ,0  ,0  ,0  ,0  },
	{'B','R','E','A','K','I','T','I','F','Y','O','U','C','A','N','!'}
};
uint8_t newKey[] =     {'B','R','E','A','K','I','T','I','F','Y','O','U','C','A','N','!'};

void setup() {
	pinMode(LED_PIN, OUTPUT);
	digitalWrite(LED_PIN, LED_OFF);
	Serial.begin(115200);
	Serial.println(F("Mifare Ultralight C test"));
	SPI.begin();
	
	Ultralight.PCD_Init();
	//Ultralight.PCD_SetAntennaGain(Ultralight.RxGain_max);
	Ultralight.PCD_DumpVersionToSerial();
	
}

void wait_for_new_card(MifareUltralight::Uid old_uid) {
	while(strncmp((char*)Ultralight.uid.uidByte, (char*)old_uid.uidByte, 7) == 0) {
		if(Ultralight.PICC_IsNewCardPresent()) {
			Ultralight.PICC_ReadCardSerial();
		}
	}
}

void loop() {
	wait_for_new_card(Ultralight.uid);
	Ultralight.PICC_DumpDetailsToSerial(&Ultralight.uid);

	bool authenticated = false;
	for(int i = 0; i < n_keys; i++) {
		Serial.print(F("Attempting to authenticate with key number "));
		Serial.println(i+1);
		MifareUltralight::StatusCode status = Ultralight.Authenticate(defaultKeys[i], true);
		if (status == MifareUltralight::STATUS_OK) {
			authenticated = true;
			break;
		}
		else {
			Serial.println(Ultralight.GetStatusCodeName(status));
			Ultralight.PICC_HaltA();
			byte bufferATQA[2];
	byte bufferSize = sizeof(bufferATQA);
			Ultralight.PICC_WakeupA(bufferATQA, &bufferSize);
			Ultralight.PICC_ReadCardSerial();
		}
	}

	if (authenticated) {
		Serial.println(F("Auth OK"));
		for (int i = 0; i <5; i++) {
			digitalWrite(LED_PIN, LED_ON);
			delay(500);
			digitalWrite(LED_PIN, LED_OFF);
			delay(500);
		}
		
	}
	else {
		Serial.println(F("Auth FAILED"));
			digitalWrite(LED_PIN, LED_ON);
			delay(3000);
			digitalWrite(LED_PIN, LED_OFF);
	}
	
}

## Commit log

2018-06-19 board release candidate
    [AccessControlBoard.brd, AccessControlBoard.sch]
2018-06-21 started firmware development
    [LabAccessBoard.brd, LabAccessBoard.sch]
2018-08-23 first woking version
    [DoorOpenerPCB.sch, DoorOpenerPCBv2.brd, DoorOpenerPCBv2.sch]
2018-09-04 new folder structure
    [LabAccessBoard.brd, LabAccessBoard.sch]
2018-09-22 pot board
    [DoorOpenerPCB.brd, DoorOpenerPCB.sch, DoorOpenerPCBv2.sch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]
2018-10-07 board update
    [LabAccessBoard.brd, LabAccessBoard.sch]
2018-11-07 pin assignment
    [DoorOpenerPCBv2.dxf, pot board diy.brd, pot board diy.dxf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]
2018-12-08 new lab access board
    [LabAccessBoard.brd, LabAccessBoard.sch]
2018-12-08 lab access board DC
    [LabAccessDC.brd, LabAccessDC.sch]
2019-01-24 management scripts
    [LabAccessBoard.dxf, stencil.dxf]
2019-02-16 added license
    [LabAccessBoard.brd, LabAccessBoard.sch, LabAccessDC.brd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]

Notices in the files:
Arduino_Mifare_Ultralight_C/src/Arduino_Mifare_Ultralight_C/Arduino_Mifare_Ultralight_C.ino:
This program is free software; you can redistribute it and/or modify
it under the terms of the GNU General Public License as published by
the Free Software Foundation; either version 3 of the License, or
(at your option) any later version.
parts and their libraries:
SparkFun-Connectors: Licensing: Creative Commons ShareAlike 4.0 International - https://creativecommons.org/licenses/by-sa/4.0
